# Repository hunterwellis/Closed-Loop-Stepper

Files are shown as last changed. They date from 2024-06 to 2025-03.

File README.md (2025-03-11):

# Closed-Loop-Stepper

A stepper motor using daisey-chained CAN and power connections. Fits on the back of NEMA17 4-wire bipolar stepper motor.

The end goal of this project is to implement a FOC agorithm to control the stepper in closed loop.

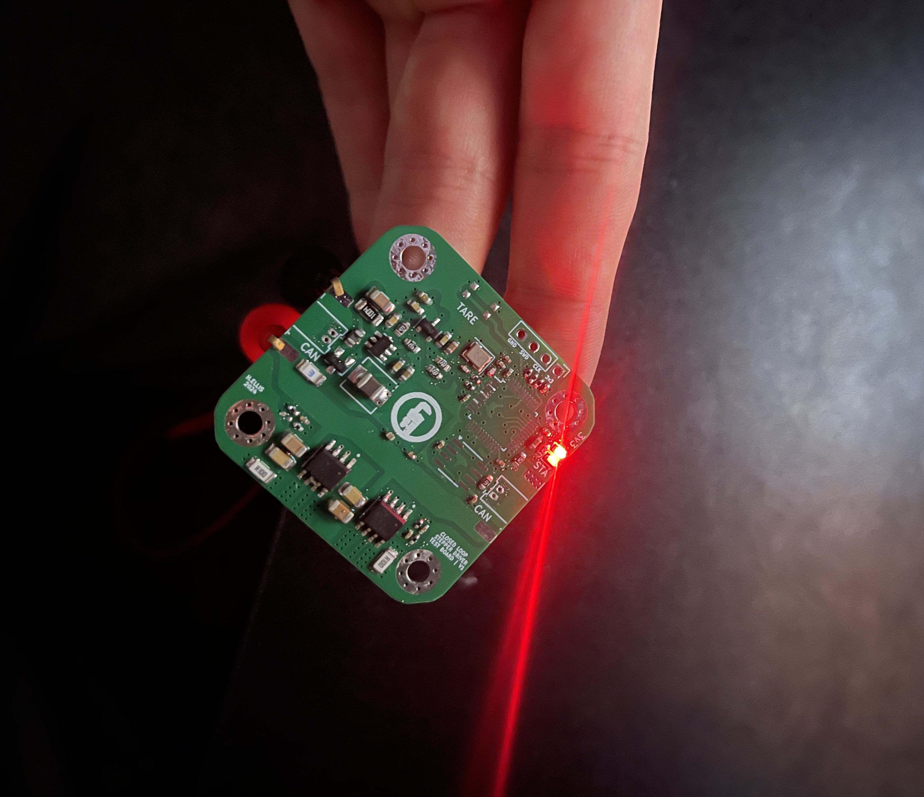
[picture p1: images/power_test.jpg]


*Image of first power test*

## Usage
Install ST and ARM-GNU toolchains.
```
sudo apt install stlink-tools gcc-arm-none-eabi
```
This the firmware for this board is written using libopencm3 (an open-sourced hardware library for ARM Cortex-M3 microcontrollers). Make sure to clone and build libopencm3 in the project repo.
```
git submodule update --init --recursive
```
This design is programmed via SWD (using an ST-Link) -- to build and flash the firmware.
```
cd ./2.Firmware/Base_Driver/src
make
st-flash --reset write base-driver.bin 0x800000
```

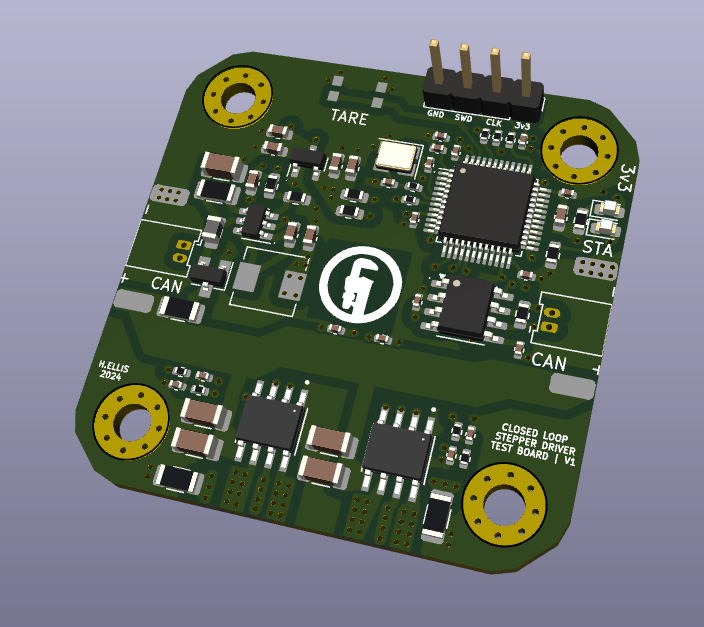
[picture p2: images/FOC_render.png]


*KiCAD render of PCBA*

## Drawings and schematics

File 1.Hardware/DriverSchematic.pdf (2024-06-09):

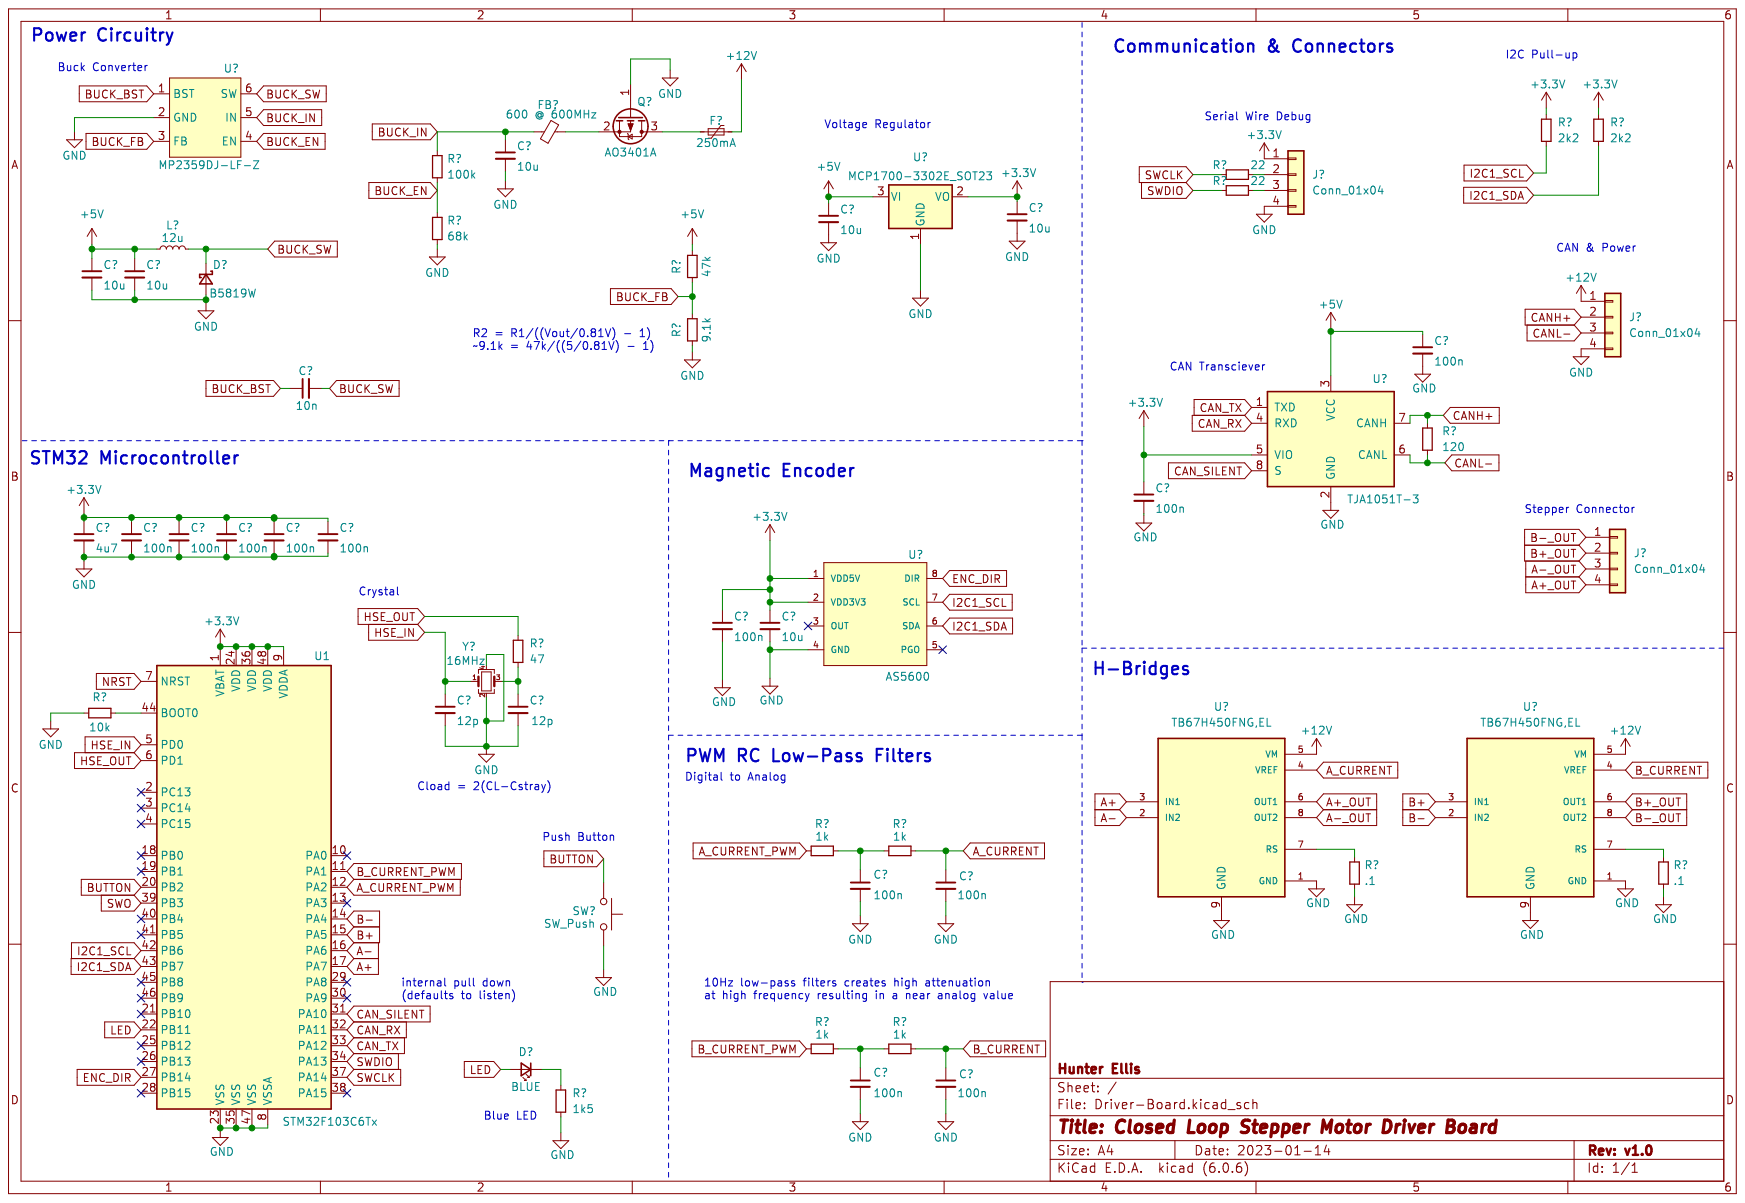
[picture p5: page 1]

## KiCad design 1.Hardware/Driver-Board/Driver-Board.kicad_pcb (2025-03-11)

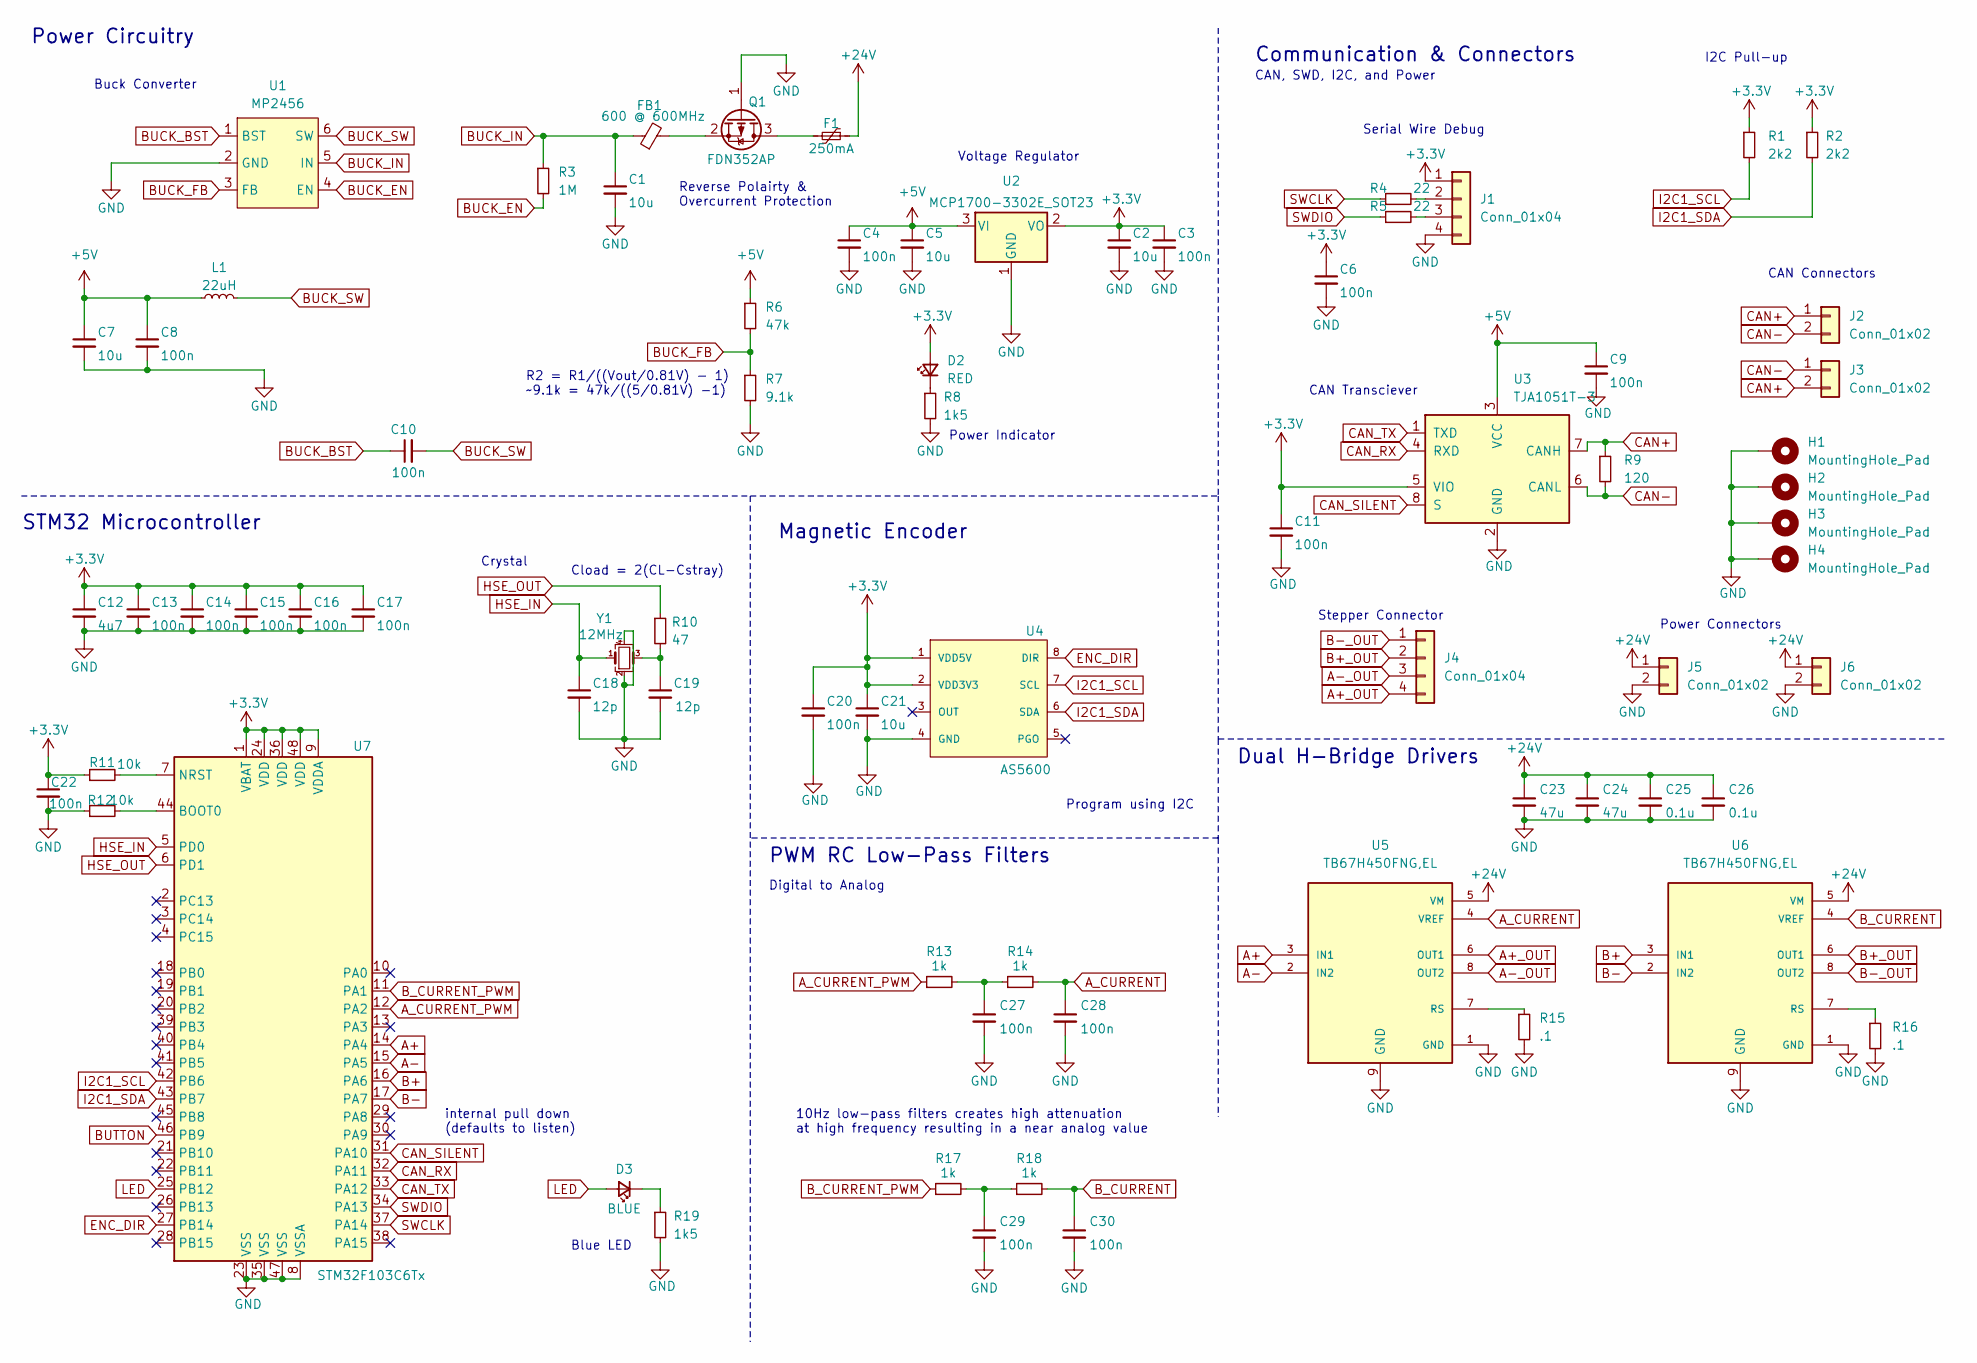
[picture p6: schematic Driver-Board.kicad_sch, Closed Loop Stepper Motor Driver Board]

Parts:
C1: 10u; C_1206_3216Metric
C2, C5, C7: 10u; C_0603_1608Metric
C3, C4, C8, C10: 100n; C_0603_1608Metric
C6, C9, C11, C13, C14, C15, C16, C17, C20, C22, C27, C28, C29, C30: 100n; C_0402_1005Metric
C12: 4u7; C_0603_1608Metric
C18, C19: 12p; C_0402_1005Metric
C21: 10u; C_0402_1005Metric
C23, C24: 47u; C_1206_3216Metric
C25, C26: 0.1u; C_1206_3216Metric
D2: RED; LED_0603_1608Metric
D3: BLUE; LED_0603_1608Metric
F1: 250mA; Fuse_1206_3216Metric
FB1: 600 @ 600MHz; L_0805_2012Metric
H1, H2, H3, H4: MountingHole_Pad; MountingHole_3.2mm_M3_Pad_Via
J1: Conn_01x04; PinHeader_1x04_P2.54mm_Vertical
J2, J3: Conn_01x02; Molex_PicoBlade_53048-0210_1x02_P1.25mm_Horizontal
J4: Conn_01x04; Stepper Wire Connector
J5, J6: Conn_01x02; 24V Split Power Connection
L1: 22uH; L_Sunlord_MWSA0518_5.4x5.2mm
Q1: FDN352AP; SuperSOT-3
R1, R2: 2k2; R_0603_1608Metric
R3: 1M; R_1206_3216Metric
R4, R5: 22; R_0402_1005Metric
R6: 47k; R_0603_1608Metric
R7: 9.1k; R_0603_1608Metric
R8, R19: 1k5; R_0603_1608Metric
R9: 120; R_0603_1608Metric
R10: 47; R_0402_1005Metric
R11, R12: 10k; R_0402_1005Metric
R13, R14, R17, R18: 1k; R_0402_1005Metric
R15, R16: .1; R_1206_3216Metric
U1: MP2456; TSOT-23-6
U2: MCP1700-3302E_SOT23; SOT-23
U3: TJA1051T-3; SOIC-8_3.9x4.9mm_P1.27mm
U4: AS5600; SOIC-8_3.9x4.9mm_P1.27mm
U5, U6: TB67H450FNG,EL; SOIC127P599X175-9N; PARTREV 3.0
U7: STM32F103C6Tx; LQFP-48_7x7mm_P0.5mm
Y1: 12MHz; Crystal_SMD_3225-4Pin_3.2x2.5mm

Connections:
+3.3V: C2.1, C3.1, C6.1, C11.1, C12.1, C13.1, C14.1, C15.1, C16.1, C17.1, C20.1, C21.1, C22.1, D2.2 (A), J1.1, R1.1, R2.1, R11.1, U2.2 (VO), U3.5 (VIO), U4.1 (VDD5V), U4.2 (VDD3V3), U7.1 (VBAT), U7.9 (VDDA), U7.24 (VDD), U7.36 (VDD), U7.48 (VDD)
+5V: C4.1, C5.1, C7.1, C8.1, C9.1, L1.1, R6.1, U2.3 (VI), U3.3 (VCC)
+24V: C23.1, C24.1, C25.1, C26.1, F1.1, J5.1, J6.1, U5.5 (VM), U6.5 (VM)
A+: U5.3 (IN1), U7.14 (PA4)
A+_OUT: J4.4, U5.6 (OUT1)
A-: U5.2 (IN2), U7.15 (PA5)
A-_OUT: J4.3, U5.8 (OUT2)
A_CURRENT: C28.1, R14.2, U5.4 (VREF)
A_CURRENT_PWM: R13.1, U7.12 (PA2)
B+: U6.3 (IN1), U7.16 (PA6)
B+_OUT: J4.2, U6.6 (OUT1)
B-: U6.2 (IN2), U7.17 (PA7)
B-_OUT: J4.1, U6.8 (OUT2)
BUCK_BST: C10.1, U1.1 (BST)
BUCK_EN: R3.2, U1.4 (EN)
BUCK_FB: R6.2, R7.1, U1.3 (FB)
BUCK_IN: C1.1, FB1.1, R3.1, U1.5 (IN)
BUCK_SW: C10.2, L1.2, U1.6 (SW)
BUTTON: U7.46 (PB9); also elsewhere on the board
B_CURRENT: C30.1, R18.2, U6.4 (VREF)
B_CURRENT_PWM: R17.1, U7.11 (PA1)
CAN+: J2.1, J3.2, R9.1, U3.7 (CANH)
CAN-: J2.2, J3.1, R9.2, U3.6 (CANL)
CAN_RX: U3.4 (RXD), U7.32 (PA11)
CAN_SILENT: U3.8 (S), U7.31 (PA10)
CAN_TX: U3.1 (TXD), U7.33 (PA12)
ENC_DIR: U4.8 (DIR), U7.27 (PB14)
GND: C1.2, C2.2, C3.2, C4.2, C5.2, C6.2, C7.2, C8.2, C9.2, C11.2, C12.2, C13.2, C14.2, C15.2, C16.2, C17.2, C18.2, C19.2, C20.2, C21.2, C22.2, C23.2, C24.2, C25.2, C26.2, C27.2, C28.2, C29.2, C30.2, H1.1, H2.1, H3.1, H4.1, J1.4, J5.2, J6.2, Q1.1 (G), R7.2, R8.2, R12.1, R15.2, R16.2, R19.2, U1.2 (GND), U2.1 (GND), U3.2 (GND), U4.4 (GND), U5.1 (GND), U5.9 (GND), U6.1 (GND), U6.9 (GND), U7.8 (VSSA), U7.23 (VSS), U7.35 (VSS), U7.47 (VSS), Y1.2, Y1.4; also elsewhere on the board
HSE_IN: C18.1, U7.5 (PD0), Y1.1
HSE_OUT: R10.1, U7.6 (PD1)
I2C1_SCL: R1.2, U4.7 (SCL), U7.42 (PB6)
I2C1_SDA: R2.2, U4.6 (SDA), U7.43 (PB7)
LED: D3.2 (A), U7.25 (PB12)
unnamed: C19.1, R10.2, Y1.3
unnamed: C27.1, R13.2, R14.1
unnamed: C29.1, R17.2, R18.1
unnamed: D2.1 (K), R8.1
unnamed: D3.1 (K), R19.1
unnamed: J1.2, R4.2
unnamed: J1.3, R5.2
unnamed: F1.2, Q1.3 (D)
unnamed: FB1.2, Q1.2 (S)
unnamed: R15.1, U5.7 (RS)
unnamed: R16.1, U6.7 (RS)
unnamed: R12.2, U7.44 (BOOT0)
unnamed: R11.2, U7.7 (NRST)
SWCLK: R4.1, U7.37 (PA14)
SWDIO: R5.1, U7.34 (PA13)

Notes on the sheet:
CAN, SWD, I2C, and Power
Reverse Polairty & Overcurrent Protection
CAN Transciever
Cload = 2(CL-Cstray)
Buck Converter
Voltage Regulator
Power Connectors
Dual H-Bridge Drivers
Blue LED
Crystal
Power Circuitry
Power Indicator
internal pull down (defaults to listen)
Magnetic Encoder
R2 = R1/((Vout/0.81V) - 1) ~9.1k = 47k/((5/0.81V) -1)
STM32 Microcontroller
CAN Connectors
Communication & Connectors
PWM RC Low-Pass Filters
Serial Wire Debug
Program using I2C
10Hz low-pass filters creates high attenuation at high frequency resulting in a near analog value
I2C Pull-up
Digital to Analog
Stepper Connector

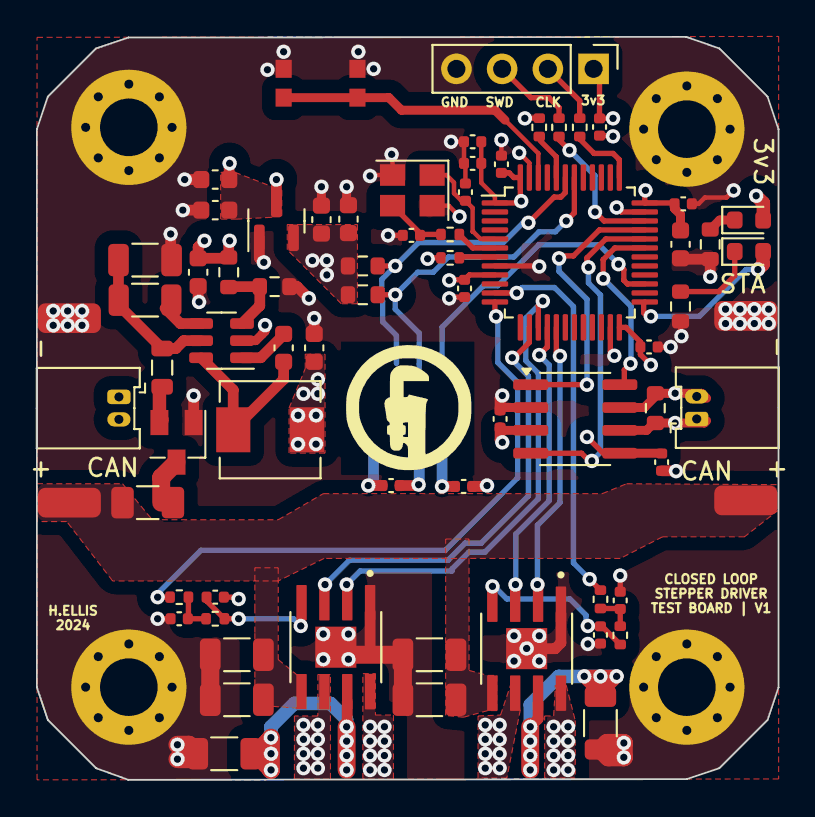
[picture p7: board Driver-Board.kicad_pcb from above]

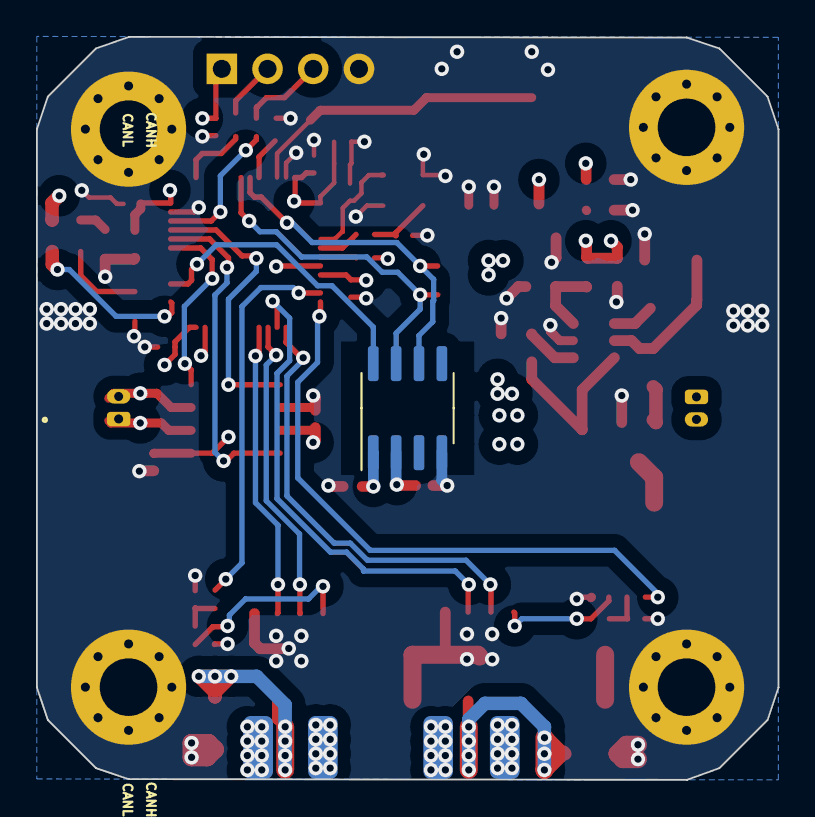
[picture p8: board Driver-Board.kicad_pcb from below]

Board: 4 copper layers, 41.2 x 41.3 mm, 74 parts (2 on the bottom side), 48 nets.

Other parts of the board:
SW1: SW_Push; KMR731NG LFS

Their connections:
BUTTON: SW1.2; also elsewhere on the board
GND: SW1.1; also elsewhere on the board

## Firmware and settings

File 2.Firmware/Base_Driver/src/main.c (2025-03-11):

#include <libopencm3/stm32/rcc.h>
#include <libopencm3/stm32/gpio.h>
#include "as5600.h"

void gpio_setup(void){

    rcc_periph_clock_enable(RCC_GPIOC);
    rcc_periph_clock_enable(RCC_GPIOA);
    
    // enable PC13 (--> LED on bluepill)
    gpio_set_mode(GPIOC,
            GPIO_MODE_OUTPUT_2_MHZ,
            GPIO_CNF_OUTPUT_PUSHPULL,
            GPIO13);

    // H-Bridge Inputs
    // A+
    gpio_set_mode(GPIOA,
            GPIO_MODE_OUTPUT_2_MHZ,
            GPIO_CNF_OUTPUT_PUSHPULL,
            GPIO4);
    // A-
    gpio_set_mode(GPIOA,
            GPIO_MODE_OUTPUT_2_MHZ,
            GPIO_CNF_OUTPUT_PUSHPULL,
            GPIO5);
    // B+
    gpio_set_mode(GPIOA,
            GPIO_MODE_OUTPUT_2_MHZ,
            GPIO_CNF_OUTPUT_PUSHPULL,
            GPIO6);
    // B-
    gpio_set_mode(GPIOA,
            GPIO_MODE_OUTPUT_2_MHZ,
            GPIO_CNF_OUTPUT_PUSHPULL,
            GPIO7);

}

static void i2c_setup(void){

    rcc_periph_clock_enable(RCC_I2C1);

    // config GPIO pins for I2C1: PB6 (SCL) & PB7 (SDA)
    gpio_set_mode(GPIOB, GPIO_MODE_OUTPUT_50_MHZ,
            GPIO_CNF_OUTPUT_ALTFN_OPENDRAIN,
            GPIO_I2C1_SCL | GPIO_I2C1_SDA);

    i2c_peripheral_disable(I2C1);

    i2c_set_clock_frequency(I2C1, AS5600_ADDR);
    i2c_set_ccr(I2C1, 180);  // CCR = PCLK1 / (2 * 100kHz)
    i2c_set_trise(I2C1, 37); // TRISE = (1/PCLK1) * 1µs + 1

    // Enable I2C1
    i2c_peripheral_enable(I2C1);

}

static void pwm_setup(void){

}

static void can_setup(void){

}

int main(void){
    
    gpio_setup();
    i2c_setup();

    while(1){
        
        /*uint8_t message = 0;*/
        /**/
        /*// start communication and send data*/
        /*i2c_send_start(I2C1);*/
        /*while (!(I2C_SR1(I2C1) & I2C_SR1_SB)); // wait for START condition */
        /**/
        /*i2c_send_7bit_address(I2C1, AS5600_ADDR, I2C_READ);*/
        /*while (!(I2C_SR1(I2C1) & I2C_SR1_ADDR)); // wait for slave ack*/
        /**/
        /*(void)I2C_SR2(I2C1); // clear ADDR flag*/
        /**/
        /*// master ack */
        /*i2c_enable_ack(I2C1);*/
        /*i2c_send_stop(I2C1);*/
        /**/
        /*while (!(I2C_SR1(I2C1) & I2C_SR1_RxNE));*/
        /*message = i2c_get_data(I2C1);*/
        /**/
        /*i2c_send_stop(I2C1); // Stop communication*/
        /**/
        /*(void)message;*/
        // blink led
        for (int i = 0; i < 1000000; i++){
            __asm__("nop");
        }
        
        gpio_toggle(GPIOC, GPIO13);

    }

    return 0;
}

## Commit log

2024-06-09 init commit
    [Driver-Board-B_Cu.gbr, Driver-Board-B_Mask.gbr, Driver-Board-B_Paste.gbr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]
2024-10-27 updated board
    [Driver-Board.kicad_pcb, Driver-Board.kicad_sch]
2024-11-08 corrected power trace
    [Driver-Board.kicad_pcb]
2024-11-11 added basic driver
2024-11-18 updated BOM
2024-11-18 init i2c
2025-03-11 libopencm3 integration and power test
    [Driver-Board.kicad_pcb, Driver-Board.kicad_sch]
